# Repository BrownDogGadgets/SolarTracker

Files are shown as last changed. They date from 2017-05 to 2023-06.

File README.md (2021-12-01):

# Solar Tracker

Files and Resources for our Dual Axis Solar Smart Tracker as well as our Single Axis "Dumb" Tracker.

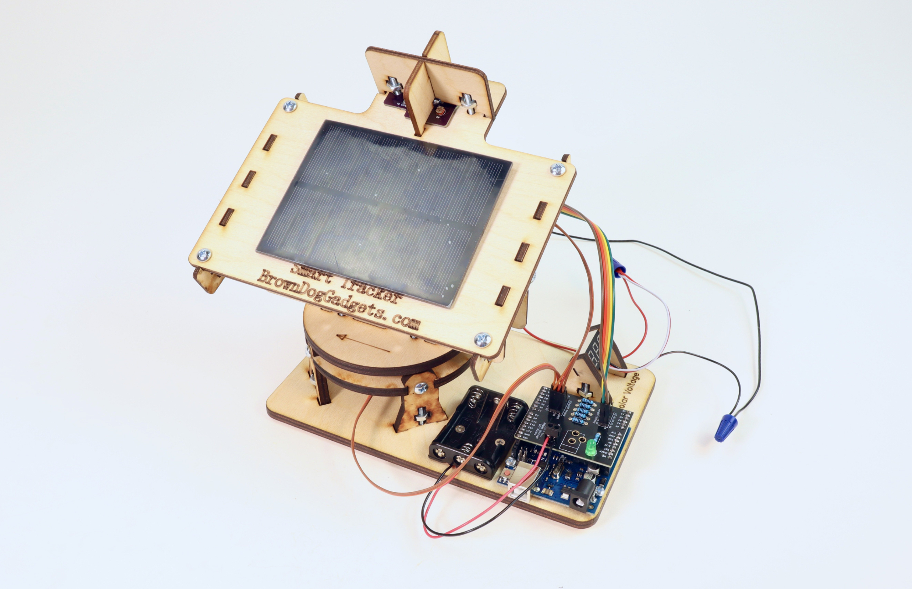
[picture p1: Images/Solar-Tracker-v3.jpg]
Solar Tracker v3


# Overview

The idea behind these projects was to create a beginner level activity that had a real world application.  The Dual Axis Tracker used a common Arduino Uno and a Sensor Shield to move two servos and follow the light.  We took inspriation and code from existing solar tracking projects on instructables.com and provided a more useful lasercut body.

After the popularity of our Dual Axis Tracker we also designed a more simple "Dumb" Tracker that used a common Metal Gear Motor (6V 35 RPM) to move along a single axis. Two small 6V 80mA solar cells acted as both sensors and power for the motor.  While less electronicly complicated the project ended up being a much more awkward and difficult build.

Version 2 of the Dual Axis Tracker streamlined the physical build by replacing about half the 1/4th inch wood pieces with 1/8th inch pieces, lowering the strain on the two servos.  A custom designed Arduino Shield and LDR Sensor holder made the electronics much easier. Version 3 is a futher refinement and uses an improved Digital I/O Shield for connecting the servos and LDR sensors to the Arduino.

A new version of the Single Axis Tracker was also designed along the same lines, going with mostly 1/8th inch wood.  Instead of using an Arduino Uno it uses a Crazy Circuits Robotics Board (Nano) as well as the same LDR Sensor holder from the V2 Dual Axis.  A single servo moves the body along a single axis.

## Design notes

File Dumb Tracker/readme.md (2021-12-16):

# Dumb Tracker

This simple tracker uses a geared mechanism to move the entire body around a stationary base.  Instead of digital sensors and a processing unit, this relies on a single geared motor and two solar cells.

The project uses  quarter inch thick material (birch plywood), a dowel rod, a common 6V 35 RPM metal gear motor, and two 6V 80mA solar cells. Additional supplies needed are screws, screw terminal blocks, wire, and rubber feet. Optional: A larger solar cell for the face and a LED volt meter.

Tool wise, you need access to a laser cutter or CNC machine able to cut quarter inch material, screw drivers, wire cutter and stripper, and a soldering iron to attach wires to the solar cells and motor.

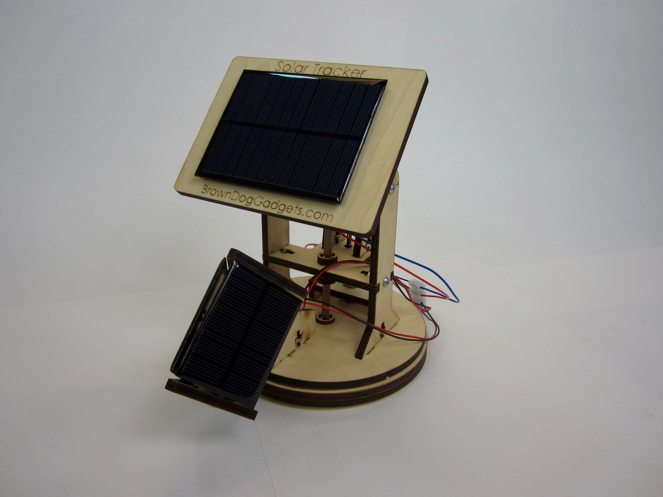
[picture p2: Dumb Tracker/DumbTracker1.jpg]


While this project works decently in good sunlight it suffers in low light conditions since it is self powering. The project is also annoying to assemble for such a simple concept.

We eventually morphed this project into the "smart" Single Axis Tracker. This proved to be a more interesting project and an easier physical build.

On a side note, we originally modeled this project on a simple YouTube video that used a motor with a rubber stopper on the shaft, two solar cells, and a lazy susan for the body. (A project much more simple than what this project morphed into.)

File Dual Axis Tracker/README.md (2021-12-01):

# Dual Axis Solar Tracker V3

For a full build guide visit: https://browndoggadgets.dozuki.com/Guide/Dual+Axis+Solar+Tracker+3.0/382

## Solar Tracker Shield and LDR Board

The new (as of October 2021) [Digital I/O Shield](hardware/Digital-IO-Arduino-Shield-Type-A-v1.1) is a general purpose Arduino shield and replaces the old version of the Solar Tracker Shield. Any Solar Tracker sold after October 2021 will use the Digital I/O Shield and will require that you use the Arduino sketch `Dual_Axis_Tracker_V3.ino`

(The old [Solar Tracker Shield](hardware/Solar-Tracker-Shield-v1.1) was used previous to the release of the Digital I/O Shield in October 2021. If you are using this older version of the Solar Tracker Shield you will need to use the Arduino sketch `Dual_Axis_Tracker_V2.ino`)

[The Light-Detecting Resistor (LDR) Board](hardware/LDR-Board) is a board with four photocells and male pin headers. It connects to the Digital I/O Shield with female jumper wires.

Both of the shields work with the Arduino Uno board and have male pin headers for connecting the servos and light detecting resistors (via female jumper wires).

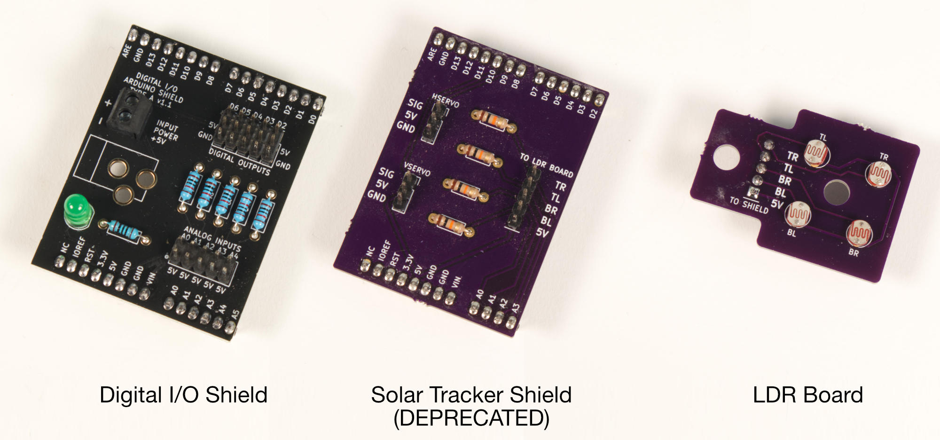
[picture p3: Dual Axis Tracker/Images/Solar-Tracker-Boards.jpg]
Solar Tracker Boards


## Test and Setup of Servos

The Arduino sketch `Servo_Test.ino` should be used to ensure your servos both work once connected to the shield. (The Arduino and shield must be powered for the servo test to work.)

The Arduino sketch `Servo_Set_Mid.ino` will set both servos to the 90 degree (mid) point and is useful to run before doing assembly of the tracker.

## Hardware

The majority of screws are 3/4th inch 8-32 pan head screws, one 1/2th inch 8-32 screw, one 2-1/2th inch 8-32 screw, along with four #2 wood screws to mount the servos, two M3 screws to mount the Arduino Uno, and two M3 screws to mount the battery holder. Rubber feet are necessary for the bottom of the base.

## Laser Cut Files

Use a laser cutter or CNC router to cut the parts out. Use 1/4th inch and 1/8th inch plywood for this project. A 1 inch by 1 inch reference square has been put on the laser cut design to to allow for adjustment if importing causes resizing problems.

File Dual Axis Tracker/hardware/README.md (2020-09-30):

# Hardware

The `LDR-Board` holds the photocells. (This board has not changed since its initial design.)

The `Solar Tracker Shield v1.1` is the _old_ version of the Solar Tracker Shield. If you are using this you will need to use the Arduino sketch `Dual_Axis_Tracker_V2.ino`

The `Digital I/O Arduino Shield Type A v1.1` is the _new_ version of our general purpose I/O shield that works with the Solar Tracker. This shield will be released in the fall of 2020. If you are using this you will need to use the Arduino sketch `Dual_Axis_Tracker_V3.ino`

The `Arduino-Nano-Board` is an _older_ version of the shield meant to work with an Arduino Nano instead of an Arduino Uno.

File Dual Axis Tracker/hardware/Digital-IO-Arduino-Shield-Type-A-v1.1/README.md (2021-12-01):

# Digital I/O Arduino Shield Type A v1.1

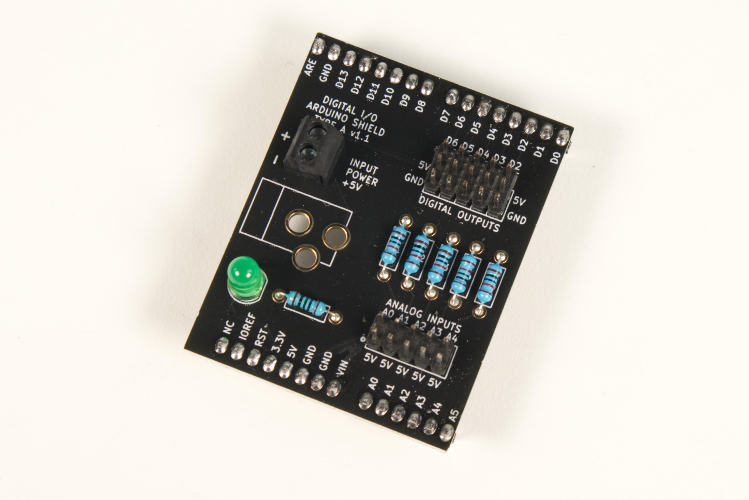
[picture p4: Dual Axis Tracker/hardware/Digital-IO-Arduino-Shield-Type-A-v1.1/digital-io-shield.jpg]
Digital I/O Shield


The **Digital I/O Shield** is a general purpose Arduino shield and replaces the old version of the Solar Tracker Shield. Any Solar Tracker sold after October 2021 will use the Digital I/O Shield and will require that you use the Arduino sketch `Dual_Axis_Tracker_V3.ino`

Make the following connections between the LDR Board and the Shield.

|LDR Board|Shield|
|---|---|
|TR|A0|
|TL|A1|
|BR|A2|
|BL|A3|

Make the following connections between the two servos and the Shield.

|Servo|Shield|
|---|---|
|Horizontal Servo|D5|
|Vertical Servo|D6|

Power the Arduino, either with a USB cable or using the barrel jack.

Power the Shield with an external 3 AAA battery pack connected to the screw terminals on the Shield. This provides power to the servos so the tracker can move.

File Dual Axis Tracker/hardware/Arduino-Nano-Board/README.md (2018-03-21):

<!--- start title --->
# Solar Tracker Arduino Nano Board v1.5
A Lego-compatible Crazy Circuits module

- Updated: 21 Mar 2018

- Website: http://browndoggadgets.com/
- Company: Brown Dog Gadgets
- License: All rights reserved.
<!--- end title --->

This is the main board that sits on the Arduino, reads in the light sensors, and commands the servos to move the solar tracker. It has holes for four M3 screws and it uses the Arduino Nano microcontroller.

<!--- bom start --->
### Bill of Materials

|Ref|Qty|Description|Digikey PN|
|---|---|---|---|
|J1 J2|2|HEADER MALE 3POS TH 1x03 0.1IN|952-1902-ND|
|J3|1|CONN TERM SCREW GREEN 2.54MM 5POS TH|ED10564-ND|
|R1 R2 R3 R4|4|RES 10K OHM 1/4W 5% CF MINI|S10KQCT-ND|
|U1|1|ARDUINO NANO BOARD|1050-1001-ND|

<!--- bom end --->

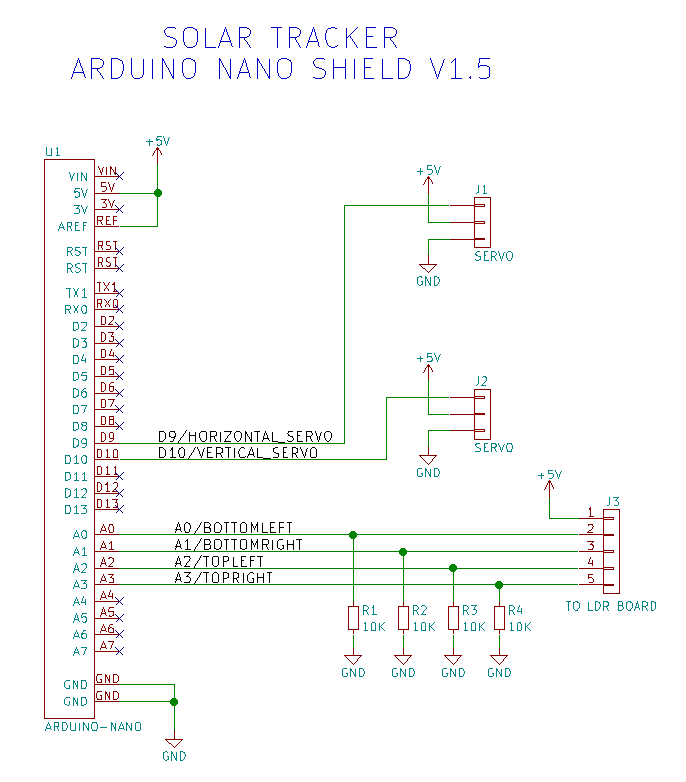
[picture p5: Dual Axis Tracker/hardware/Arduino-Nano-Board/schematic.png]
Schematic


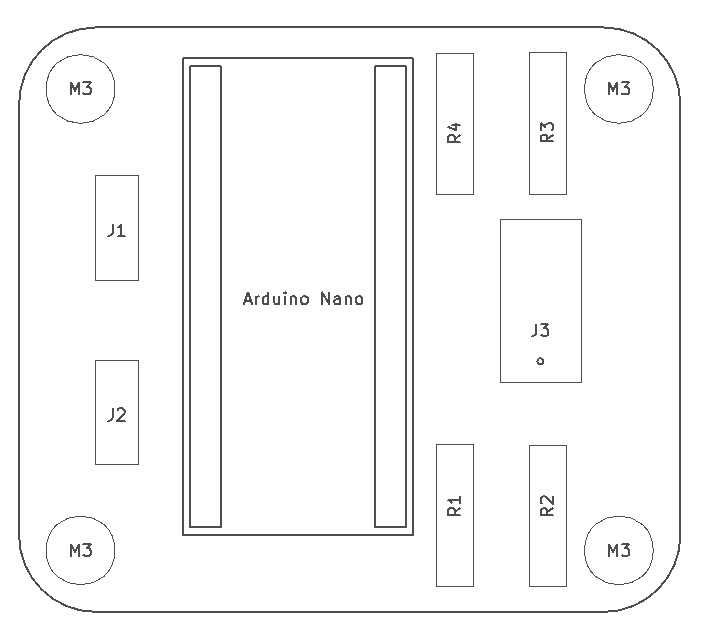
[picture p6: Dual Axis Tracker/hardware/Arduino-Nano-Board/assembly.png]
Assembly Diagram


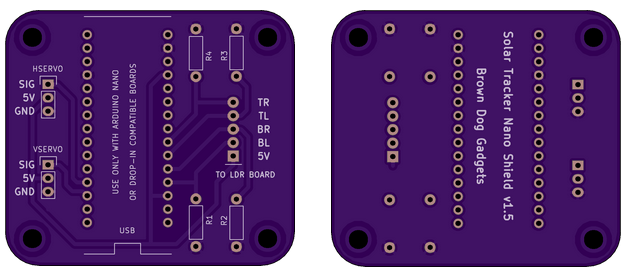
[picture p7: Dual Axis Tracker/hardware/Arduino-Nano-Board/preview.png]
Gerber Preview


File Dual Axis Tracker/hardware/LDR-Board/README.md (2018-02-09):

<!--- start title --->
# Solar Tracker Light Sensing Board v1.3

- Updated: 9 Feb 2018
- Website: http://browndoggadgets.com/
- Company: Brown Dog Gadgets
- License: All rights reserved.
<!--- end title --->

This photocell board board sits on the tracker itself. This version adds a second 0.2" unplated screw hole.

<!--- bom start --->
### Bill of Materials

|Ref|Qty|Description|Digikey PN|
|---|---|---|---|
|J1|1|CONN TERM SCREW GREEN 2.54MM 5POS TH|ED10564-ND|
|R1 R2 R3 R4|4|PHOTOCELL 3K-11K OHM 5.10MM|PDV-P8001-ND|

<!--- bom end --->
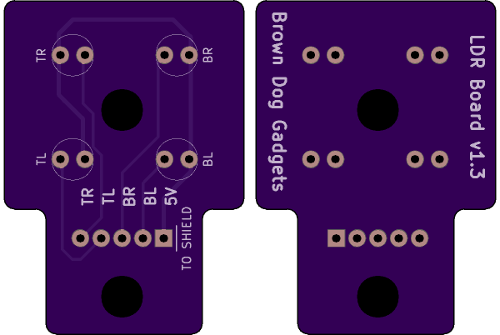
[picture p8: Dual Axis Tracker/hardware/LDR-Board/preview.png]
Gerber Preview


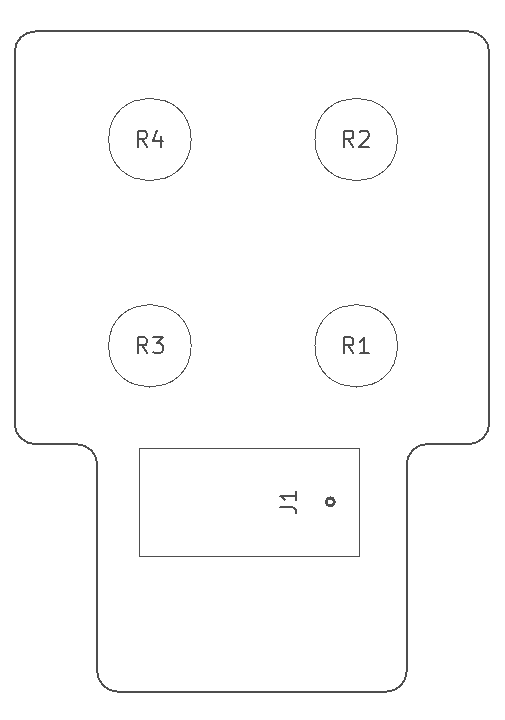
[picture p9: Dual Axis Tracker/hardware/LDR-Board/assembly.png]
Assembly Diagram


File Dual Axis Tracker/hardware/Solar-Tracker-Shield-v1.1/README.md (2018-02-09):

<!--- start title --->
# Solar Tracker Arduino Shield v1.1

- Updated: 9 Feb 2018
- Website: http://browndoggadgets.com/
- Company: Brown Dog Gadgets
- License: All rights reserved.
<!--- end title --->

This is the main board that sits on the Arduino, reads in the light sensors, and commands the servos to move the solar tracker.

<!--- bom start --->
### Bill of Materials

|Ref|Qty|Description|Digikey PN|
|---|---|---|---|
|J1 J2|2|HEADER MALE 3POS TH 1x03 0.1IN|952-1902-ND|
|J3|1|CONN TERM SCREW GREEN 2.54MM 5POS TH|ED10564-ND|
|R1 R2 R3 R4|4|RES 10K OHM 1/4W 5% CF MINI|S10KQCT-ND|
|U1|1|HEADERS MALE BREAKAWAY 0.1IN|S1012EC-26-ND|

<!--- bom end --->
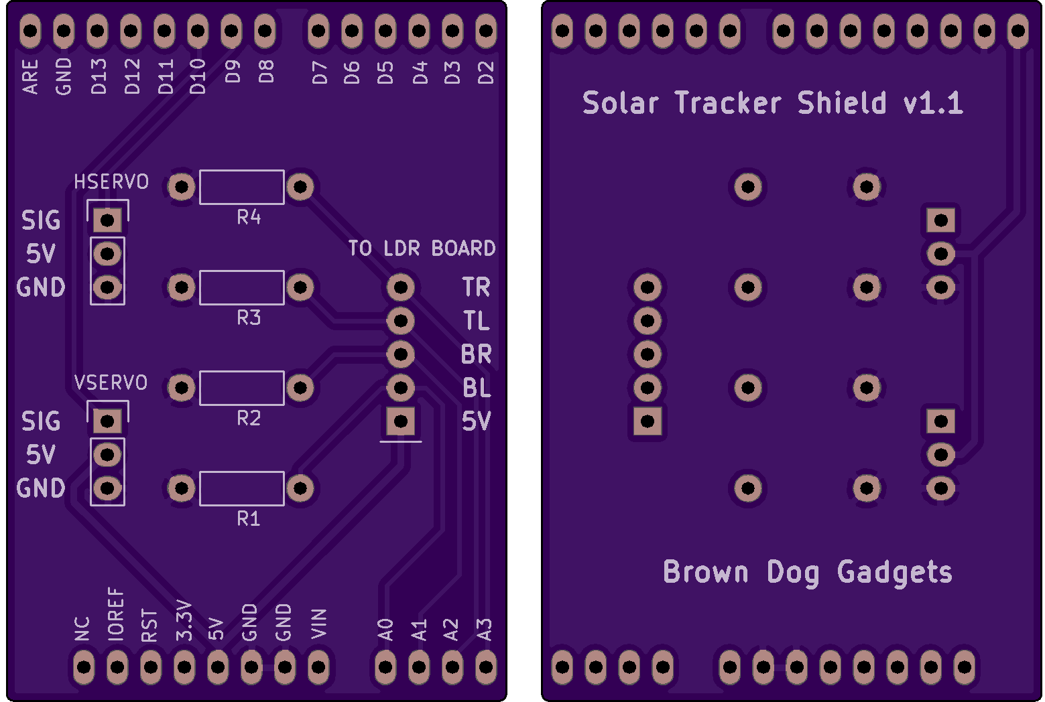
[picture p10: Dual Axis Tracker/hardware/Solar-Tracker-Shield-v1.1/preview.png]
Gerber Preview
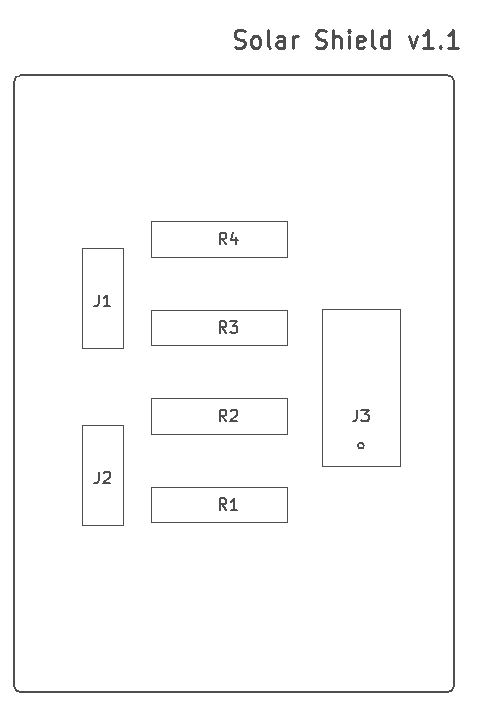
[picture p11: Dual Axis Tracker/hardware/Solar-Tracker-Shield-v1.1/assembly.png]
Assembly Diagram


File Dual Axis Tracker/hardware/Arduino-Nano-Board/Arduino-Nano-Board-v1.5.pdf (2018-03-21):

Crazy Circuits | Brown Dog Gadgets

# Solar Tracker Arduino Nano Board v1.5

## A Lego-compatible Crazy Circuits module

This is the main board that sits on the Arduino, reads in the light sensors, and commands the servos to move the solar tracker. It has holes for four M3 screws and it uses the Arduino Nano microcontroller.

Bill of Materials

Ref | Qty | Description | Digikey PN
J1 J2 | 2 | HEADER MALE 3POS TH 1x03 0.1IN | 952-1902-ND
J3 | 1 | CONN TERM SCREW GREEN 2.54MM 5POS TH | ED10564-ND
R1 R2 R3 R4 | 4 | RES 10K OHM 1/4W 5% CF MINI | S10KQCT-ND
U1 | 1 | ARDUINO NANO BOARD | 1050-1001-ND


March 21, 2018 | Solar Tracker Arduino Nano Board v1.5

Crazy Circuits | Brown Dog Gadgets

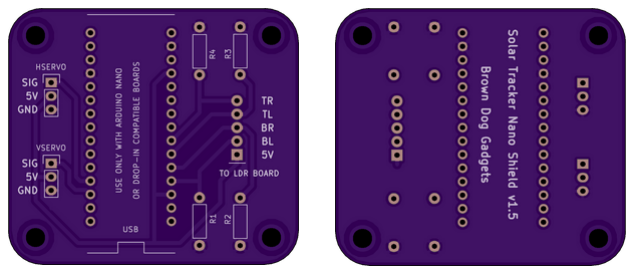
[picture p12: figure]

March 21, 2018 | Solar Tracker Arduino Nano Board v1.5

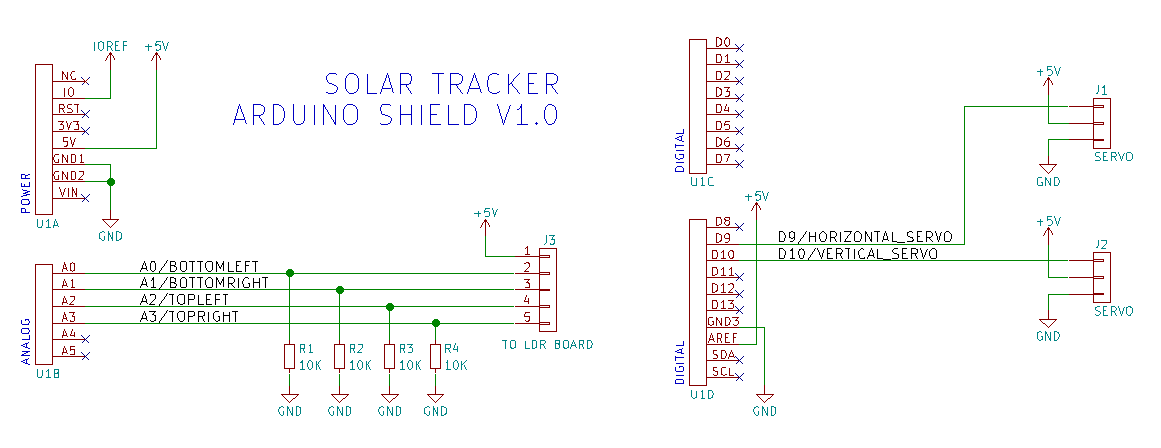
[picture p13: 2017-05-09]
Dual Axis Tracker/hardware/Solar-Tracker-Shield-v1.1/schematic.png

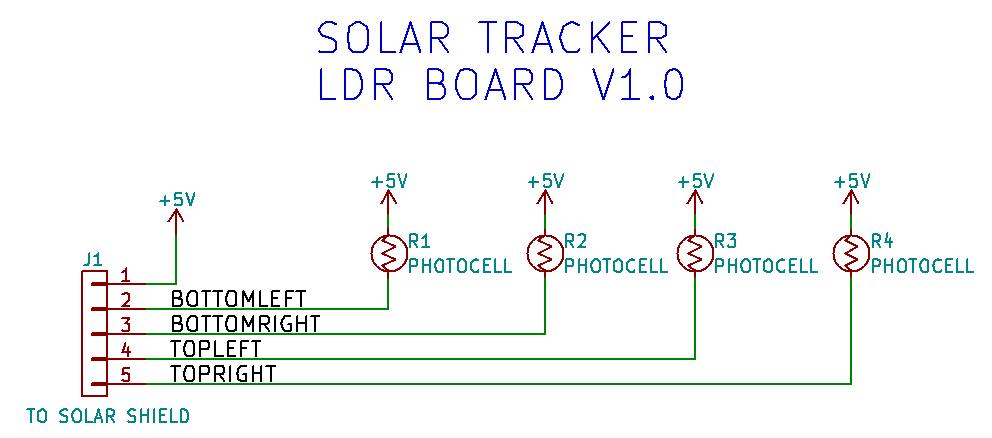
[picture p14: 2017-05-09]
Dual Axis Tracker/hardware/LDR-Board/schematic.png

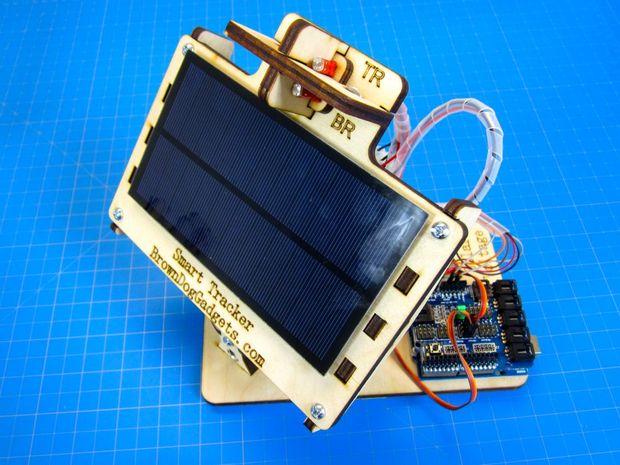
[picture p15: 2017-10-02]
Images/DualAxisV1.jpg

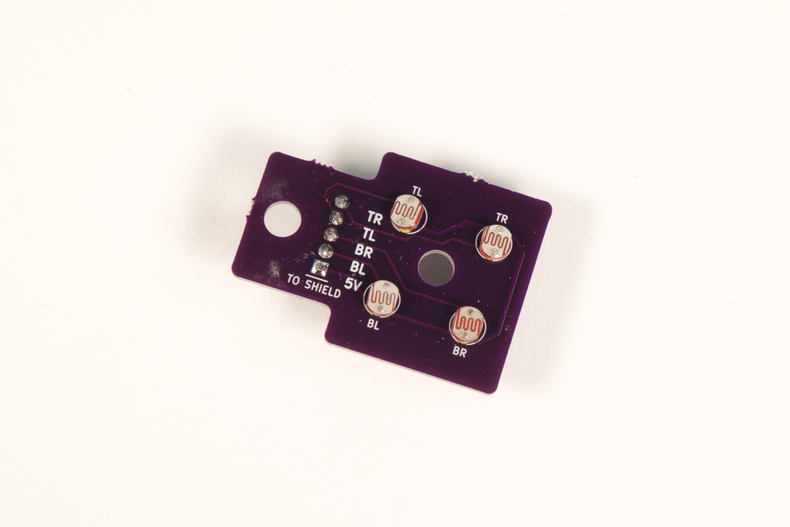
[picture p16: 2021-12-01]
Dual Axis Tracker/Images/LED-Board.jpg

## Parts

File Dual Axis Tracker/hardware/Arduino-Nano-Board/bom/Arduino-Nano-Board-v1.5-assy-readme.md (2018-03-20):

Individual Placements per board: 4

Number of Parts: 8

Board size is 2.15 x 1.90 inches (54.61 x 48.26 mm)

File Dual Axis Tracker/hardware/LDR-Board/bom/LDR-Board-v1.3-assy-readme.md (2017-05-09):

Individual Placements per board: 2

Number of Parts: 5

Board size is 1.15 x 1.60 inches (29.21 x 40.64 mm)

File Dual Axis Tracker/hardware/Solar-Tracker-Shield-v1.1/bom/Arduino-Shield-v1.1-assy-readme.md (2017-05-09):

Individual Placements per board: 4

Number of Parts: 8

Board size is 1.49 x 2.09 inches (37.85 x 53.09 mm)

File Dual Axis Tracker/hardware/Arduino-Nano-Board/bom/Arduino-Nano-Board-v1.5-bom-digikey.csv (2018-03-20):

Ref | Qty | Qty3 | Description | Digikey PN
J1 J2 | 2 | 6 | HEADER MALE 3POS TH 1x03 0.1IN | 952-1902-ND
J3 | 1 | 3 | CONN TERM SCREW GREEN 2.54MM 5POS TH | ED10564-ND
R1 R2 R3 R4 | 4 | 12 | RES 10K OHM 1/4W 5% CF MINI | S10KQCT-ND
U1 | 1 | 3 | ARDUINO NANO BOARD | 1050-1001-ND

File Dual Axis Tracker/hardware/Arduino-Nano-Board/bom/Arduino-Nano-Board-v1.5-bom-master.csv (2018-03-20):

Ref | Qty1 | Qty3 | Footprint | Footprint Library | Symbol | Symbol Library | Datasheet | MF_Name | MF_PN | S1_Name | S1_PN | Type
J1 J2 | 2 | 6 | CONN-HEADER-STRAIGHT-P2.54MM-1x03 | Wickerlib | HEADER-MALE-3POS-TH-1x03-P0.1IN | crazy_circuits | https://cdn.harwin.com/pdfs/60page140.pdf | Harwin | M20-9992046 | Digikey | 952-1902-ND
J3 | 1 | 3 | CONN-ONSHORE-SCREW-GREEN-5PIN-TH | Wickerlib | CONN-TERM-SCREW-GREEN-2.54MM-5POS-TH | wickerlib | http://www.on-shore.com/sites/default/files/manuals/ostvnxxa150.pdf | OnShoreTech | OSTVN05A150 | Digikey | ED10564-ND
R1 R2 R3 R4 | 4 | 12 | RES-CARBONFILM-7MM | Wickerlib | RES-10K-5%-1/4W-TH-CFMINI | wickerlib | http://www.seielect.com/catalog/SEI-CF_CFM.pdf | Stackpole | CFM14JT10K0 | Digikey | S10KQCT-ND
U1 | 1 | 3 | ARDUINO-NANO | Crazy_NonLego | ARDUINO-NANO-RESCUE-Arduino-Nano-Board | Arduino-Nano-Board-rescue | https://www.pjrc.com/teensy/ | Arduino | A000005 | Digikey | 1050-1001-ND

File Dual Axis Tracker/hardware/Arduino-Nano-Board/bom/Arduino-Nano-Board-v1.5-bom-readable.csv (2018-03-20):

Ref | Qty | Qty3 | Description | MF | MF_PN | S1 | S1_PN | Type
J1 J2 | 2 | 6 | HEADER MALE 3POS TH 1x03 0.1IN | Harwin | M20-9992046 | Digikey | 952-1902-ND
J3 | 1 | 3 | CONN TERM SCREW GREEN 2.54MM 5POS TH | OnShoreTech | OSTVN05A150 | Digikey | ED10564-ND
R1 R2 R3 R4 | 4 | 12 | RES 10K OHM 1/4W 5% CF MINI | Stackpole | CFM14JT10K0 | Digikey | S10KQCT-ND
U1 | 1 | 3 | ARDUINO NANO BOARD | Arduino | A000005 | Digikey | 1050-1001-ND

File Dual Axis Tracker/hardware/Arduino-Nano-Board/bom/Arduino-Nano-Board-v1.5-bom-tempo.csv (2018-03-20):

Refdes | Quantity | Description | Manufacturer | MPN
J1 J2 | 2 | HEADER MALE 3POS TH 1x03 0.1IN | Harwin | M20-9992046
J3 | 1 | CONN TERM SCREW GREEN 2.54MM 5POS TH | OnShoreTech | OSTVN05A150
R1 R2 R3 R4 | 4 | RES 10K OHM 1/4W 5% CF MINI | Stackpole | CFM14JT10K0
U1 | 1 | ARDUINO NANO BOARD | Arduino | A000005

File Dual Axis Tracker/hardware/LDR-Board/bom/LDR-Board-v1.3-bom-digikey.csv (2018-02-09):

Ref | Qty | Qty3 | Description | Digikey PN
J1 | 1 | 3 | CONN TERM SCREW GREEN 2.54MM 5POS TH | ED10564-ND
R1 R2 R3 R4 | 4 | 12 | PHOTOCELL 3K-11K OHM 5.10MM | PDV-P8001-ND

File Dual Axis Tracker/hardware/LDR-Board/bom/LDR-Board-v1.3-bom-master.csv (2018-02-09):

Ref | Qty1 | Qty3 | Footprint | Footprint Library | Symbol | Symbol Library | Datasheet | MF_Name | MF_PN | S1_Name | S1_PN | Type
J1 | 1 | 3 | CONN-ONSHORE-SCREW-GREEN-5PIN-TH | Wickerlib | CONN-TERM-SCREW-GREEN-2.54MM-5POS-TH | wickerlib | http://www.on-shore.com/sites/default/files/manuals/ostvnxxa150.pdf | OnShoreTech | OSTVN05A150 | Digikey | ED10564-ND
R1 R2 R3 R4 | 4 | 12 | PHOTOCELL-5.1MM | Wickerlib | PHOTOCELL-3-11KOHM-5.10MM-PDV-P8001 | wickerlib | http://advancedphotonix.com/wp-content/uploads/PDV-P8001.pdf | Luna Opto | PDV-P8001 | Digikey | PDV-P8001-ND

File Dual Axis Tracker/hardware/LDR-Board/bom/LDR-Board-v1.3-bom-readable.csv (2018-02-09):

Ref | Qty | Qty3 | Description | MF | MF_PN | S1 | S1_PN | Type
J1 | 1 | 3 | CONN TERM SCREW GREEN 2.54MM 5POS TH | OnShoreTech | OSTVN05A150 | Digikey | ED10564-ND
R1 R2 R3 R4 | 4 | 12 | PHOTOCELL 3K-11K OHM 5.10MM | Luna Opto | PDV-P8001 | Digikey | PDV-P8001-ND

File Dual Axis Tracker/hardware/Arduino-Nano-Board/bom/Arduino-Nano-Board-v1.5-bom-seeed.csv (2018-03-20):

Location | MPN/Seeed SKU | Quantity
J1 J2 | M20-9992046 | 2
J3 | OSTVN05A150 | 1
R1 R2 R3 R4 | CFM14JT10K0 | 4
U1 | A000005 | 1

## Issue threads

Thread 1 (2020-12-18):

Missing Laser Cut For Solar Voltage Mount

DjAnu, 2020-12-18:
Hi Seems Like V2 Laser cut file doesn't have drawing for Solar Voltage panel mount, Can you  please update that ?

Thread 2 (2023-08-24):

Code not working in arduino nano

MHD8441, 2023-08-24:
I have made the same design using laser cutting and assembled all the components as guided in the video, I have used arduino NANO instead of UNO and same sensor shield of NANO but when i have done uploading the code its not working. Please resolve and tell the solution.

Thank you
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

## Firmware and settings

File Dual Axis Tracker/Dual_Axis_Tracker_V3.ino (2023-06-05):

/*
 * Dual_Axis_Tracker_V3.ino
 *
 * Brown Dog Gadgets <https://www.browndoggadgets.com/>
 * 
 */

// include Servo library
#include <Servo.h>

// horizontal servo
Servo horizontal;
int servoh = 90;

int servohLimitHigh = 180;
int servohLimitLow = 65;

Servo vertical;
int servov = 90;

int servovLimitHigh = 120;
int servovLimitLow = 15;


// LDR pin connections
int ldrTR = 0; // LDR top right
int ldrTL = 1; // LDR top left
int ldrBR = 2; // LDR bottom right
int ldrBL = 3; // LDR bottom left


void setup() {
  Serial.begin(9600);
  // servo connections
  horizontal.attach(5);
  vertical.attach(6);
  // move servos
  horizontal.write(90);
  vertical.write(45);
  delay(3000);
}


void loop() {

  int tr = analogRead(ldrTR); // top right
  int tl = analogRead(ldrTL); // top left
  int br = analogRead(ldrBR); // bottom right
  int bl = analogRead(ldrBL); // bottom left

  int dtime = 0; // change for debugging only
  int tol = 50;

  int avt = (tl + tr) / 2; // average value top
  int avd = (bl + br) / 2; // average value bottom
  int avl = (tl + bl) / 2; // average value left
  int avr = (tr + br) / 2; // average value right

  int dvert = avt - avd;  // check the difference of up and down
  int dhoriz = avl - avr; // check the difference of left and right


  // send data to the serial monitor if desired
  Serial.print(tl);
  Serial.print(" ");
  Serial.print(tr);
  Serial.print(" ");
  Serial.print(bl);
  Serial.print(" ");
  Serial.print(br);
  Serial.print("  ");
  Serial.print(avt);
  Serial.print(" ");
  Serial.print(avd);
  Serial.print(" ");
  Serial.print(avl);
  Serial.print(" ");
  Serial.print(avr);
  Serial.print("  ");
  Serial.print(dtime);
  Serial.print("   ");
  Serial.print(tol);
  Serial.print("  ");
  Serial.print(servov);
  Serial.print("   ");
  Serial.print(servoh);
  Serial.println(" ");


  // check if the difference is in the tolerance else change vertical angle
  if (-1 * tol > dvert || dvert > tol) {
    if (avt > avd) {
      servov = ++servov;
      if (servov > servovLimitHigh) {
        servov = servovLimitHigh;
      }
    }
    else if (avt < avd) {
      servov = --servov;
      if (servov < servovLimitLow) {
        servov = servovLimitLow;
      }
    }
    vertical.write(servov);
  }

  // check if the difference is in the tolerance else change horizontal angle
  if (-1 * tol > dhoriz || dhoriz > tol) {
    if (avl > avr) {
      servoh = --servoh;
      if (servoh < servohLimitLow) {
        servoh = servohLimitLow;
      }
    }
    else if (avl < avr) {
      servoh = ++servoh;
      if (servoh > servohLimitHigh) {
        servoh = servohLimitHigh;
      }
    }
    else if (avl = avr) {
      // nothing
    }
    horizontal.write(servoh);
  }
  
  delay(dtime);
  
}

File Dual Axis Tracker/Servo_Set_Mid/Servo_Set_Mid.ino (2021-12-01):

/*
 * Servo_Set_Mid.ino
 *
 * Brown Dog Gadgets <https://www.browndoggadgets.com/>
 * 
 * NOTE: If you are using a Solar Tracker with the older shield you will 
 * need to change the numbers 5 and 6 below to 9 and 10 in the setup.
 * 
 */

#include <Servo.h>

Servo horizontal;
Servo vertical;

void setup() {
  horizontal.attach(5);
  vertical.attach(6);
  horizontal.write(90);
  vertical.write(90);
}

void loop() { }

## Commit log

2017-02-14 Add Solar Tracker Shield files.
    [Solar_Tracker_Shield-B.Cu.gbl, Solar_Tracker_Shield-B.Mask.gbs, Solar_Tracker_Shield-B.SilkS.gbo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]
2017-05-09 Split new LDR and old Solar Tracker boards.
    [Arduino-Shield-B.Cu.gbl, Arduino-Shield-B.Mask.gbs, Arduino-Shield-B.Paste.gbp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]
2017-05-09 Remove old project. Update docs.
    [Arduino-Shield.sch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]
2017-05-09 LDR Board v1.2 has two screw holes.
    [LDR-Board-B.Cu.gbl, LDR-Board-B.Mask.gbs, LDR-Board-B.Paste.gbp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]
2017-10-01 Reorganized
    Organization
    [Arduino-Shield-B.Cu.gbl, Arduino-Shield-B.Mask.gbs, Arduino-Shield-B.Paste.gbp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]
2017-10-01 Organization
    Changed some file names
    [Arduino-Shield-B.Cu.gbl, Arduino-Shield-B.Mask.gbs, Arduino-Shield-B.Paste.gbp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]
2018-02-09 Increased resistor length, v1.1 Arduino Shield
    [Arduino-Shield-B.Cu.gbl, Arduino-Shield-B.Mask.gbs, Arduino-Shield-B.Paste.gbp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]
2018-02-09 Release v1.3 LDR Board, wider photocell pins
    [LDR-Board-B.Cu.gbl, LDR-Board-B.Mask.gbs, LDR-Board-B.Paste.gbp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]
2018-03-20 Release Nano Shield v1.0
    [Arduino-Nano-Board-B.Cu.gbl, Arduino-Nano-Board-B.Mask.gbs, Arduino-Nano-Board-B.Paste.gbp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]
2018-03-21 Update to v1.5, number change only
    [Arduino-Nano-Board-B.Cu.gbl, Arduino-Nano-Board-B.Mask.gbs, Arduino-Nano-Board-B.Paste.gbp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]
2018-03-21 Fixed version number on schematic
    [Arduino-Nano-Board.sch]
2020-09-30 Updated with new files and code
    Addition of Digital-IO-Arduino-Shield-Type-A-v1.1 and Dual_Axis_Tracker_V3.ino
    [Arduino-Shield-B.Cu.gbl, Arduino-Shield-B.Mask.gbs, Arduino-Shield-B.Paste.gbp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]
2021-06-17 Update J1 footprint with 1.3mm holes
2021-06-17 Update photocell FP with 3.4mm spacing
2021-06-17 Generate gerbers for v 1.3.1
    [LDR-Board-B.Cu.gbl, LDR-Board-B.Mask.gbs, LDR-Board-B.Paste.gbp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]
2021-07-06 fix silkscreen labeling
    [LDR-Board.kicad_pcb]
2021-07-06 change version on silk
    [LDR-Board.kicad_pcb]
2021-12-01 Added lasercut files
